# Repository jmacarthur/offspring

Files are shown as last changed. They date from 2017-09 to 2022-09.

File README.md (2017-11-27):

# Millihertz Model F ("Offspring")

This is a project to create a working replica of the Manchester small-scale experimental machine, otherwise known as the Manchester Baby.

It will be implemented fully mechanically, that is, without any electronic or electric components. All power must be taken from a single rotating shaft input.

The finished machine should be a complete, binary-compatible implementation of the original SSEM, capable of running the same programs.

It will be significantly slower than the original machine. It is meant to operate at about one cycle every 10 seconds (100mHz) compared to the 1kHz+ operation of the original machine.

The machine is not intended to be a useful tool; it's done mainly for fun, and to act as a visual demonstration of the operation of a stored-program computer.

## Overview diagram

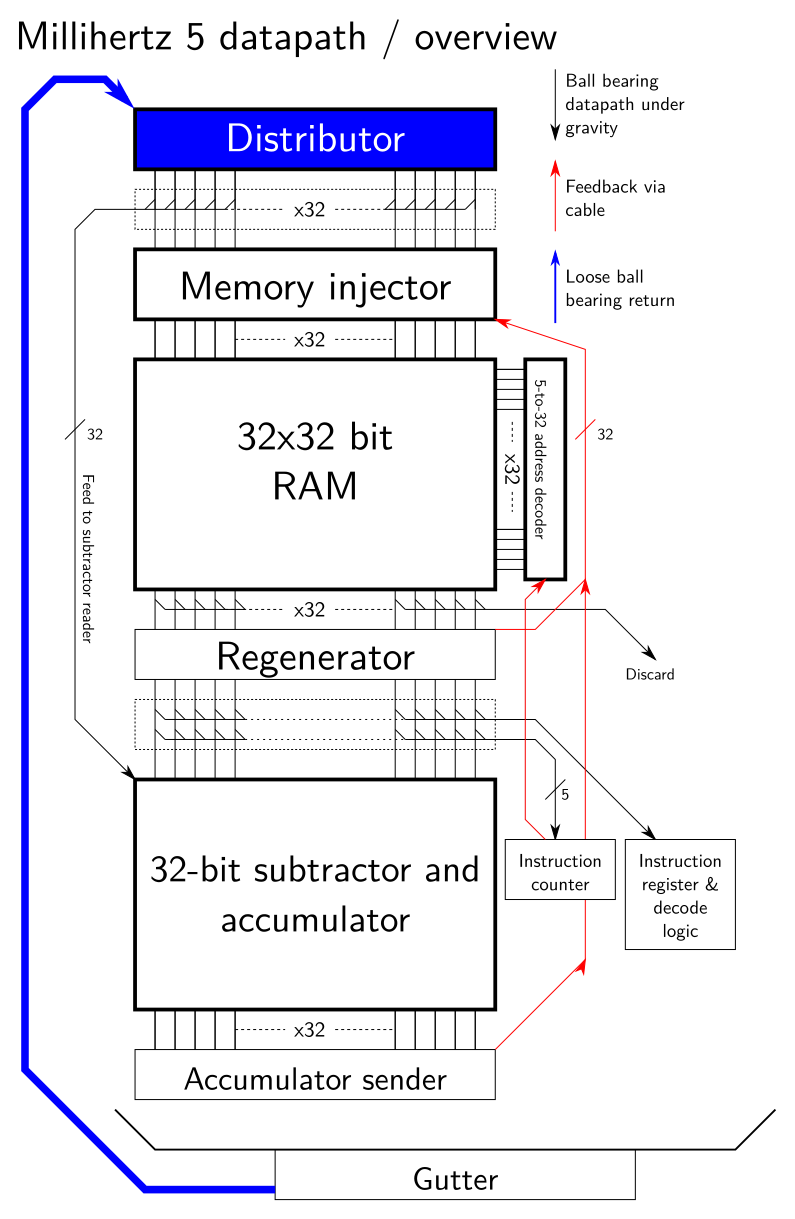
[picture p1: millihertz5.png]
Overview diagram


The machine is organised to take as much advantage of gravity as possible. The datapath runs down the machine, from the distributor at the top to the memory and then into the subtractor and accumulator. It is 32 bits wide, as was the original SSEM.

The major parts of the design have their own description pages in `docs/`.

* [Memory](docs/vertical-memory.md) - a 32x32 bit random-access memory, with address decoder.
* [Subtractor-accumulator](docs/subtractor-accumulator.md) - remembers its current value and subtracts whatever ball bearings are passed to it - a ball bearing in column 4 subtracts 16 from the accumulator, for example. Subtraction is the only arithmetic operation needed.

Parts not yet described are:

* The distributor, at the top of the machine, which measures out exactly 32 ball bearings and spreads them apart so they are the right pitch to enter the memory cell
* The memory injector, which allows selected ball bearings into the memory. There are 32 cables or rods connecting the regenerator (below) to the injector. When one is pulled down, the injector releases one of the ball bearings (which came out of the distributor) into the memory. There's also a separate control to discard any unused ball bearings in the injector.
* The regenerator samples the data coming out of the memory and pulls the rods leading to the injector, effectively sending the same pattern back into the top of the memory. This is important as reading is a destructive operation on the current memory.
* A series of diverters can send the data to the subtractor-accumulator, or the program counter, or the instruction register.
* A second regenerator below the subtractor-accumulator reads the values in the accumulator and sends them to the injector, for use in store operations.

Finally, at the bottom, all discarded ball bearings are collected and recirculated (perhaps by conveyor belt) to the distributor.

# Directories

* `scad` - CAD files in OpenSCAD format
* `diagrams` - high-level 2D drawings in DXF format for reference - showing interfaces between parts as well as some concept sketches.
* `docs` - Descriptions of parts with illustrative (not authoritative) diagrams, and reports on past experiments and prototypes.
* `lasercut-tests` - Laser cutting files generated from OpenSCAD are committed here to go alongside reports on prototypes in the `docs` directory. These should not be used other than as a reference for those documents.

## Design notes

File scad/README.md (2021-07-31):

# Index of OpenSCAD files

## Components, roughly in order from top to bottom

* octo-distributor-5.scad - current combined injector which can selectively pass ball bearings into memory and divert them to the subtractor.
* vertical-memory-2.scad - current candidate for vertical, 8x8 memory.
* decoder.scad - 16 word memory address decoder, placed alongside the memory.
* planar-diverter.scad - for diverting memory output to accumulator, PC and instruction decoder, and also the first regenerator
* subtractor.scad - subtractor/accumulator unit, used for both the main accumulator and PC
* memory-sender-3.scad - transmits memory addresses back up to the decoder.
* sequencer.scad - Main timing cam and instruction decoder.

## Assemblies

TBC

## Library files

* regenerator.scad - Common parts for the two regenerators.
* globs.scad - Constants for all files, such as the diameter of ball bearings.
* generic_conrods.scad - for producing rounded rectangles (stadia) with holes in each end, used as connecting rods.
* interconnect.scad - for connecting Bowden cables to other moving parts.

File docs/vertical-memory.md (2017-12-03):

# Vertical memory unit

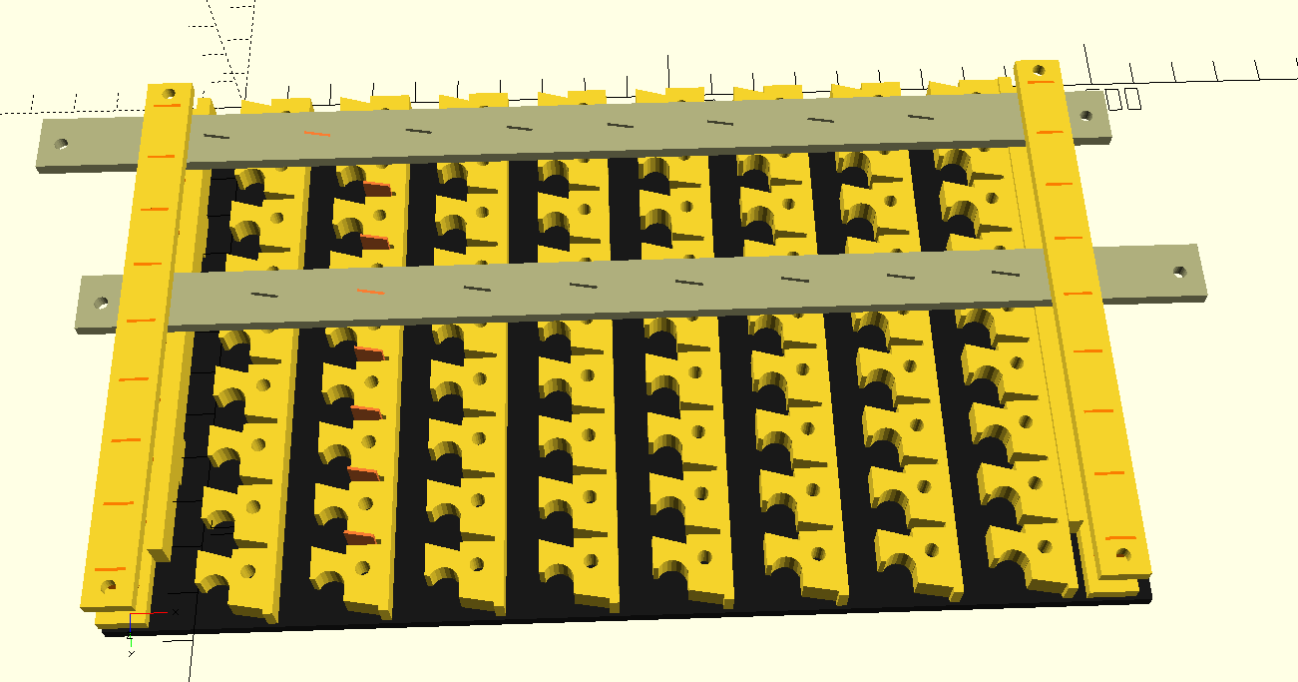
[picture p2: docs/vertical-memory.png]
Vertical memory rendering


The above rendering shows an example 8x8 memory cell. Two grey 'row select' bars are shown - there would normally be eight, but most have been removed to show the working. Most of these row select bars are pushed to the right. One, the selected row, is pushed to the left. Eight short strips of brass are embedded into the selector bars, which normally sit in a small pocket in the RAM. When pushed right, the brass strips enter the long channels in the memory, where they will intercept ball bearings rolling down that channel.

The following GIF (made with box2djs) shows the priciple of operation, for a 4x4 cell:

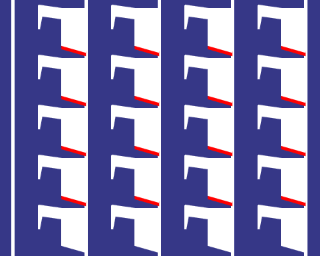
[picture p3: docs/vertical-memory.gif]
Vertical memory animation


To write data into the memory, one row is selected by pushing the corresponding row left, and a pattern of ball bearings is dropped into the channels running down the memory. A ball bearing represents a binary '1' and no ball bearing represents zero. When the ball bearings reach the selected row, the ball bearing is deflected right and into a small storage area.

When the selected row is returned to its normal position, the brass strip passes underneath the captured ball bearing, lifting it slightly but leaving it in its position.

The ball bearings remain in that row until the same row is selected again. When a row is selected while there is data in it, that data is pushed to the left and falls down the channel and out of the bottom of the RAM module. In that manner, the data stored when the row was initially selected is now read out of the memory. Reading is destructive; if you want to keep the same value in memory, you must duplicate the pattern of ball bearings and feed into the top of the RAM unit again. Magnetic core memory also had destructive reads, and regenerated memory locations in a similar way.

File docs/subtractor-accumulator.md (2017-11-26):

# Subtractor-accumulator unit

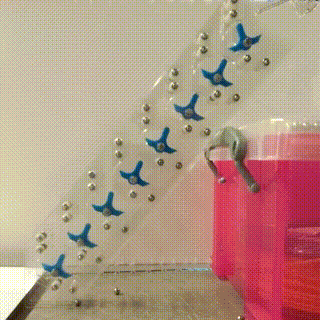
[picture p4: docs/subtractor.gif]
Subtractor video


The subtractor-accumulator sits below the memory, after the memory discard and splitters which divert to the intruction counter and register. The inverted T-shaped pieces rotate left or right to represent 1 or 0 respectively. Dropping a ball bearing into any of the input columns subtracts that value from the accumulator (the right hand column is 1, and the left 128). Subtracting 1 from 0 results in the ball bearing falling left and into the next column, so it leaves 1 in its original column and subtracts twice its value from the next column to the left. This continues until the ball bearing subtracts 1 from 1, at which point it falls to the right, or overflows out of the left of the machine.

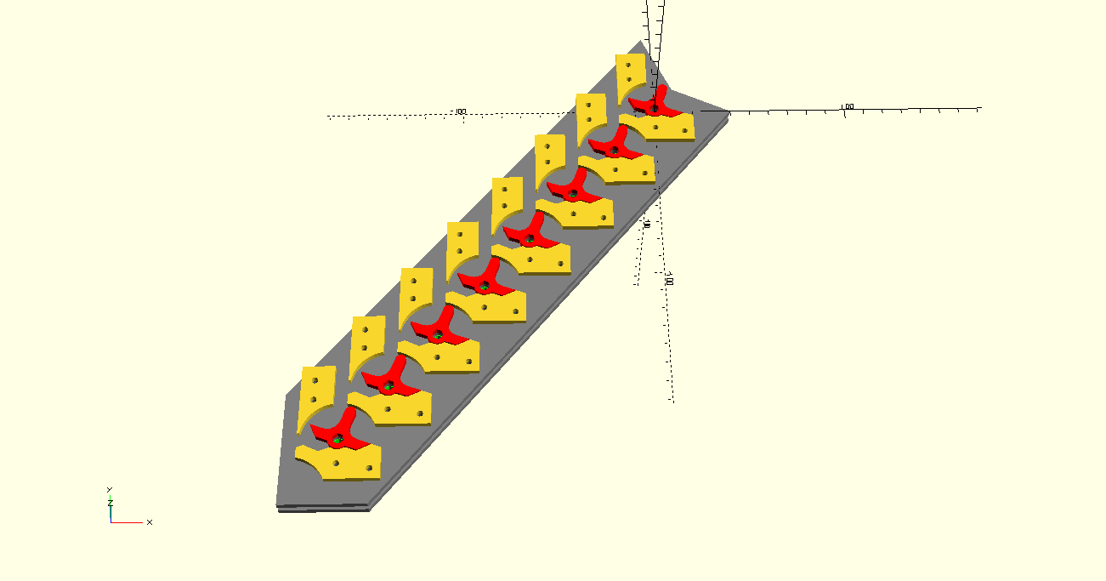
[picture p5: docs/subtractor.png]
Subtractor rendering


The design of the subtractor means it maintains its value automatically, so it's not necessary to keep a separate acumulator.

This is not my own design; there are several examples of cascading binary adders like this on the internet (TODO: where?). I've made a couple of modifications: The input senses are reversed so it functions as a subtractor rather than an adder, and it also has a second plane which can be used to copy the value in it without altering it. This requires 32 ball bearings to be dropped in on the 'read' plane, and these also come from the distributor, via the diverter valve just below it.

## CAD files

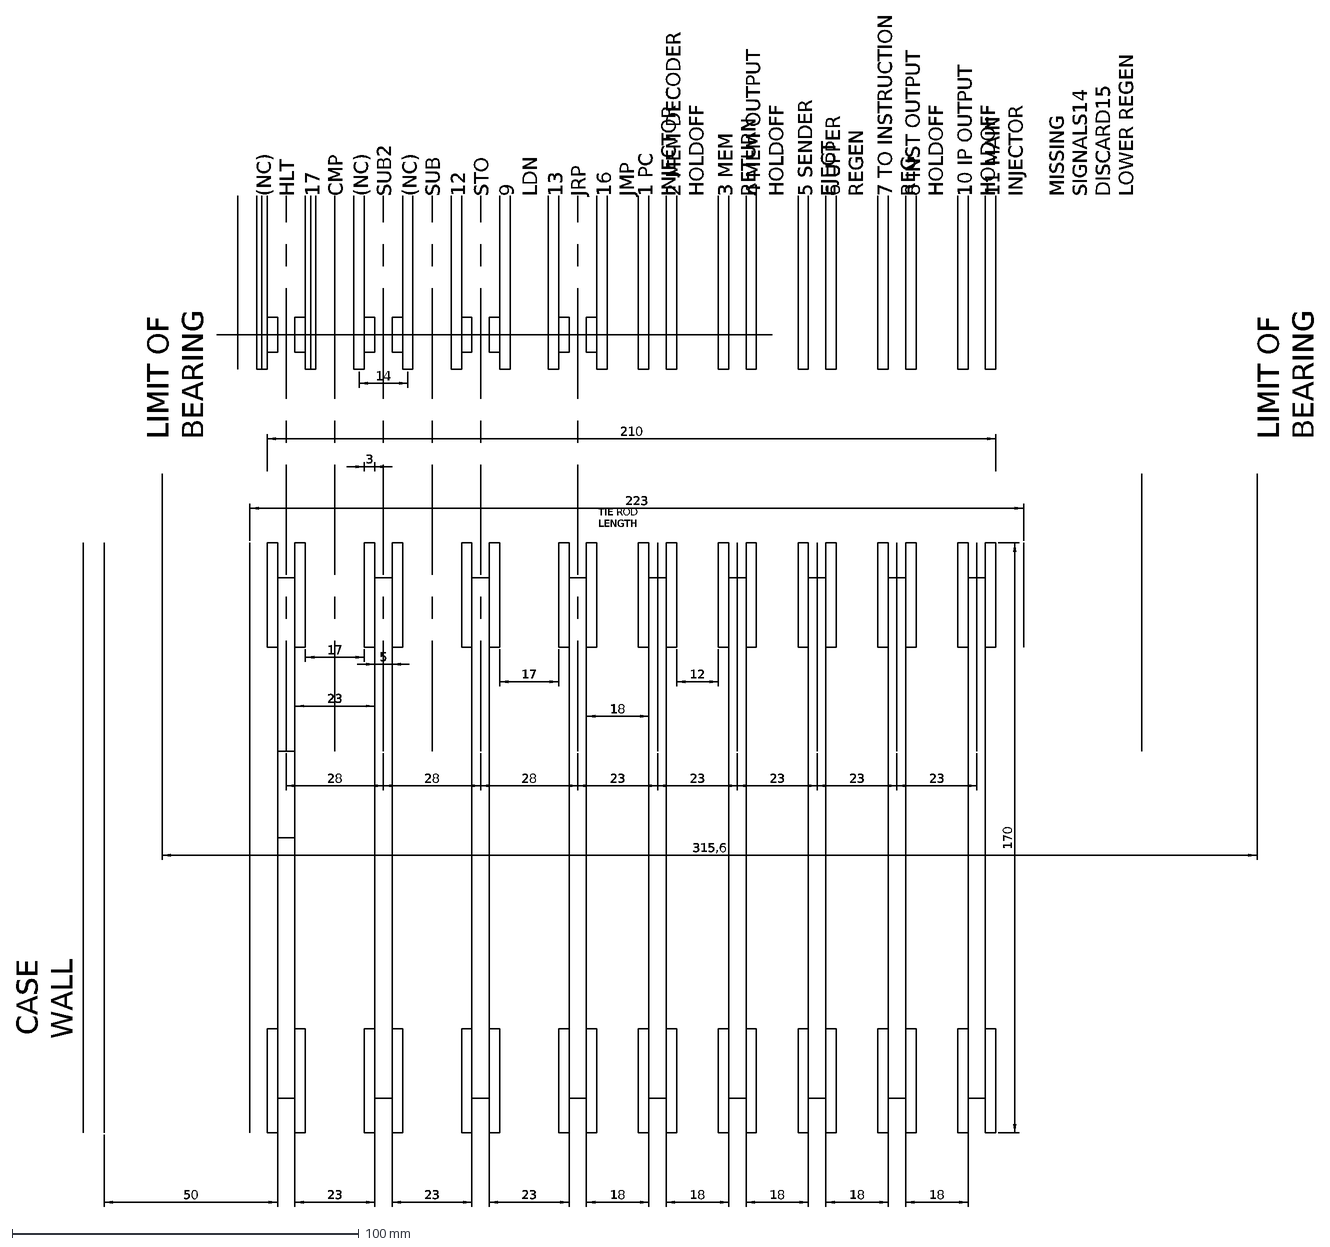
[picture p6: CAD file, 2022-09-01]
diagrams/camshaft2.dxf
28
3
14
23
210
LIMIT OF BEARING
315,6
18
5
17
12
170
16 JMP
13 JRP
9 LDN
12 STO
(NC) SUB
(NC) SUB2
17 CMP
(NC) HLT
223
TIE ROD LENGTH
1 PC INJECTOR
2 MEM DECODER HOLDOFF
3 MEM RETURN
4 MEM OUTPUT HOLDOFF
5 SENDER EJECT
6 UPPER REGEN
7 TO INSTRUCTION REG
8 INST OUTPUT HOLDOFF
10 IP OUTPUT HOLDOFF
11 MAIN INJECTOR
MISSING SIGNALS 14 DISCARD 15 LOWER REGEN
CASE WALL
50

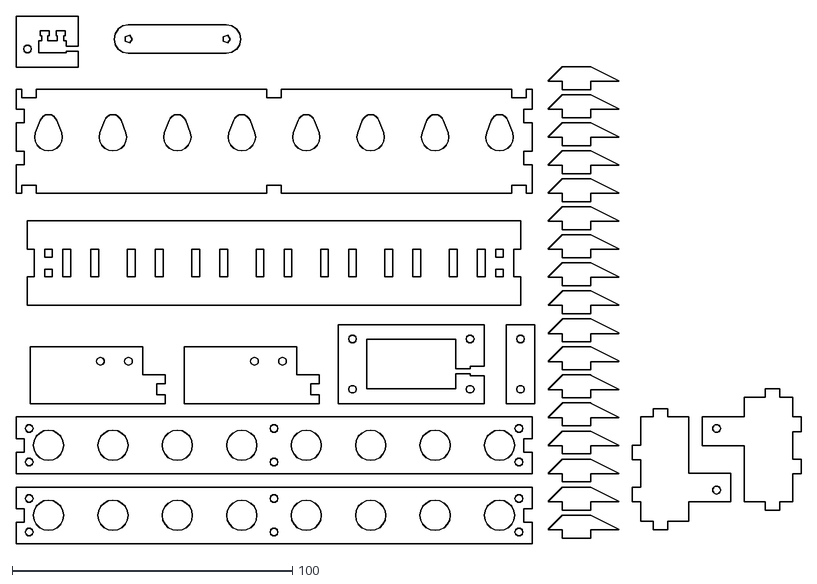
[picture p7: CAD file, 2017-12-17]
lasercut_tests/diverter-laser.dxf
280.2 x 188.2

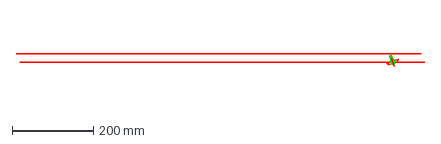
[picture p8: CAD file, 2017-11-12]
toggles.dxf
1008.0 x 30.4 mm

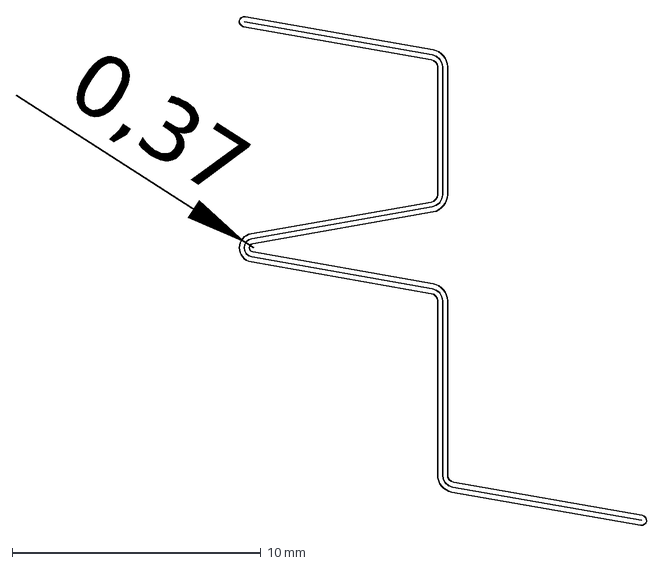
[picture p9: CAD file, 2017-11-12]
f-shape.dxf
0,37

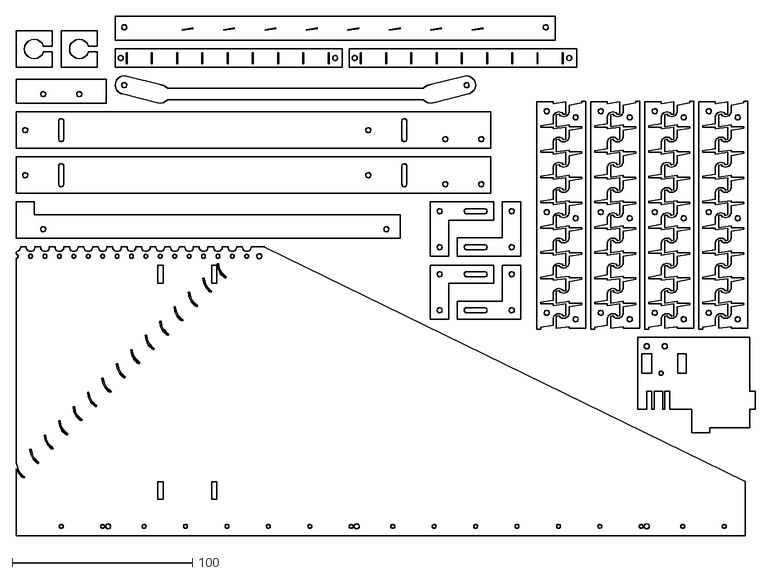
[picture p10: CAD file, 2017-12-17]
lasercut_tests/distributor-laser-2.dxf
410.2 x 288.2

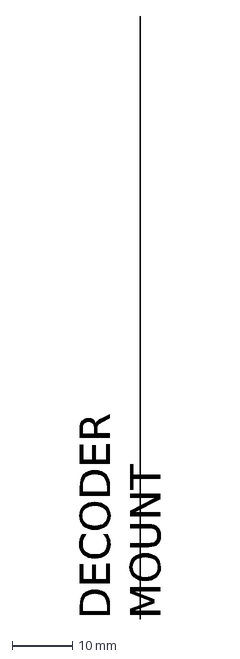
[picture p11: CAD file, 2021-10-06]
diagrams/memory-sender-mounting.dxf
DECODER MOUNT

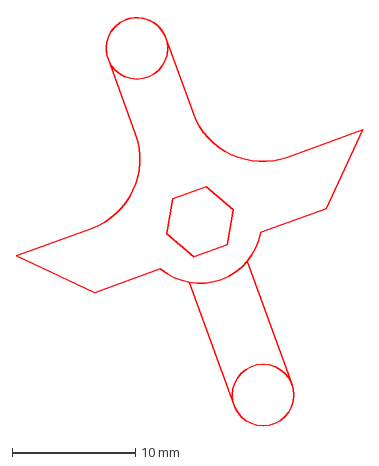
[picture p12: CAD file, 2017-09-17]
input-toggle.dxf
28.2 x 33.3 mm

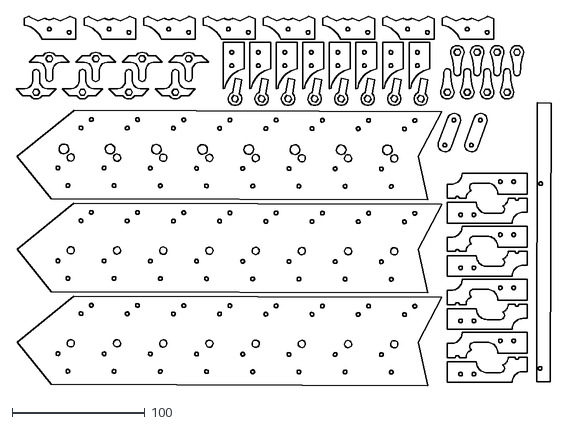
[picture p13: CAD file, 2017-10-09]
lasercut_tests/test-subtractor-v1.dxf
403.2 x 278.2

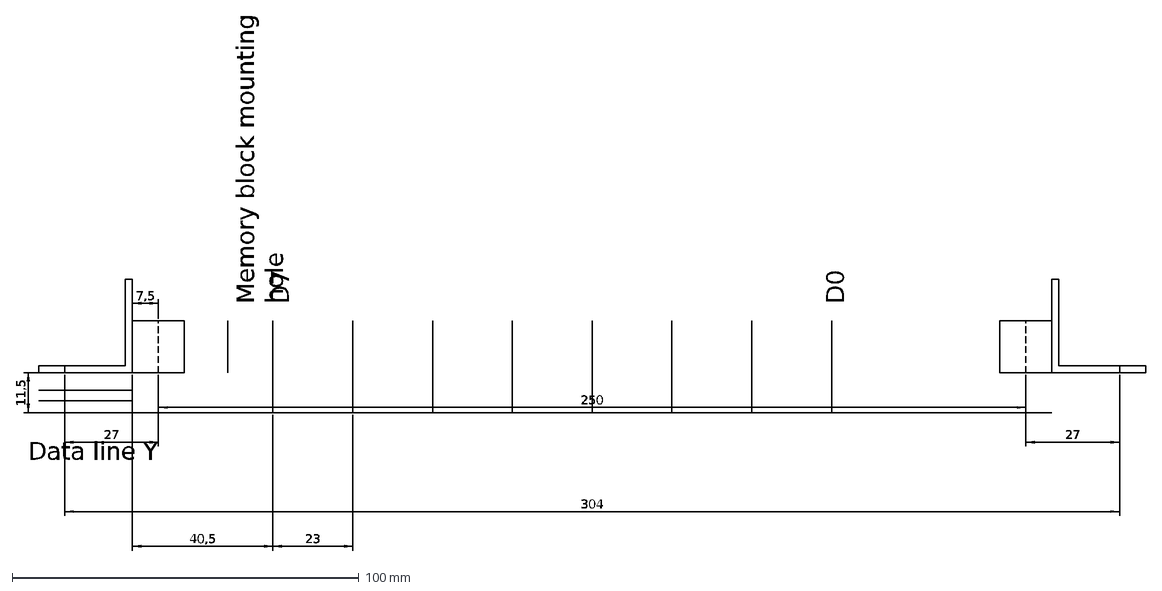
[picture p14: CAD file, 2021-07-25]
diagrams/rail_mouting.dxf
250
27
304
7,5
Memory block mounting hole
Data line Y
D7
D0
40,5
11,5
23

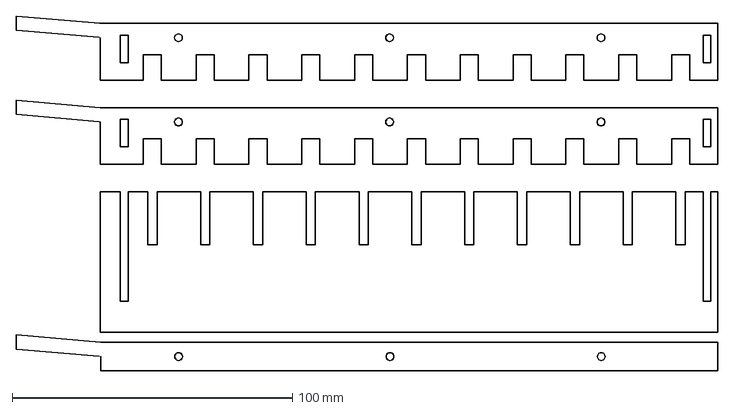
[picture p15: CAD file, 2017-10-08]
lasercut_tests/test-injector-v2.dxf
250.3 x 126.6 mm

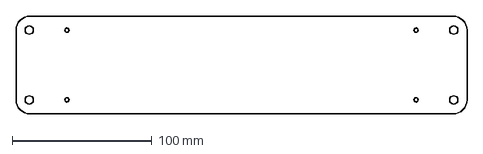
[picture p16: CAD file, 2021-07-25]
diagrams/rail_separator_plate.dxf
323.0 x 70.0 mm

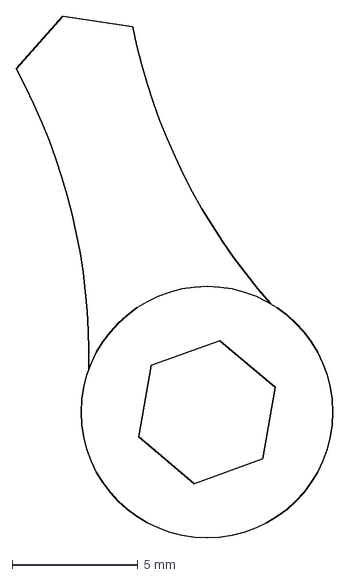
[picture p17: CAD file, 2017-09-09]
output-toggle.dxf
12.6 x 20.7 mm

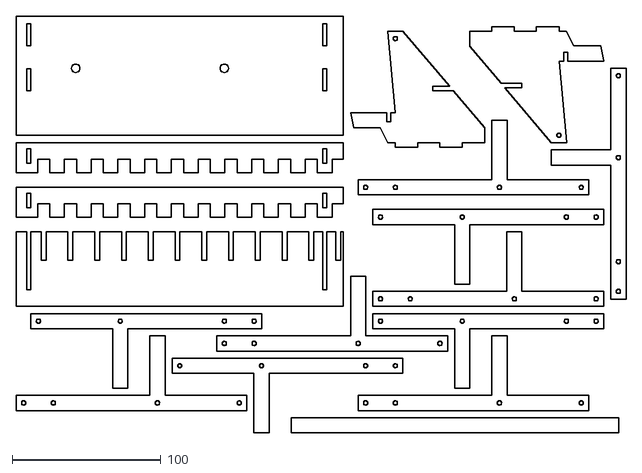
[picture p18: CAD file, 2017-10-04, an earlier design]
lasercut_tests/test-injector-v1.dxf
410.2 x 280.2

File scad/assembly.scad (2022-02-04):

use <vertical-memory-2.scad>;
use <octo-distributor-6.scad>;
use <regen-diverter.scad>;
use <decoder.scad>;
include <globs.scad>;
use <infra.scad>;
use <stacked-subtractor.scad>;
use <base-regen.scad>;

use <sequencer.scad>;
use <memory-sender-4.scad>;
module memory_mounting_plate() {
  x1 = 100; // coord of first openbeam rail centre
  x2 = x1+20; // coord of first memory mounting hole
  y1 = 280;
  difference() {
    cube([420,5,300]);
    // Openbeam mounting holes
    translate([x1,-1,y1]) rotate([-90,0,0]) cylinder(d=3,h=10);
    translate([x1+250,-1,y1]) rotate([-90,0,0]) cylinder(d=3,h=10);

    // Memory mounting holes
    translate([x2,-1,y1]) rotate([-90,0,0]) cylinder(d=3,h=10);
    translate([x2+200,-1,y1]) rotate([-90,0,0]) cylinder(d=3,h=10);
    // Decoder mounting holes
    for(y=[0:2])
    translate([x1+250+47, -1, y1-17.5-119*y]) rotate([-90,0,0]) cylinder(d=10,h=10);
  }
}


module openbeam() {
  color([0.3,0.3,0.3]) cube([15,15,1000]);
}
memory_mount_z = 800;

translate([0,0,1100]) injector_assembly();
translate([22.5,-5,memory_mount_z+158]) rotate([90,0,0]) memory_assembly();
translate([22.5,-5,memory_mount_z+10]) rotate([90,0,0]) memory_assembly();
translate([329.5,35,memory_mount_z+158+124.5]) rotate([0,90,0]) address_decoder();

translate([angle_iron_internal_spacing,0,0]) perforated_angle();
translate([0,0,0]) rotate([0,0,90]) perforated_angle();

openbeam();
translate([angle_iron_internal_spacing-15, 0 ,0]) openbeam();

color([0,0,0.9,0.5]) translate([-100+7.5,-5,memory_mount_z]) memory_mounting_plate();

// Indicate where memory input is
//color([0,1,1]) translate([data7_x, -11.5, 780]) cylinder(d=ball_bearing_diameter, h=50);


translate([0,0,550]) stacked_subtractor();

translate([0,-28,300]) rotate([0,0,-90]) base_regen(0);

translate([0,-130,100]) {
  sequencer_assembly();
  casing();
}

translate([350,30,350]) sender();

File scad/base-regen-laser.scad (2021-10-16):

use <base-regen.scad>;


backing_plate_2d();
kerf = 0.08;
$fn=50;


offset(r=kerf) {
  translate([0,50]) 
    for(i=[0:15]) {
      translate([i*20,0]) rotate(90) input_coupler_2d();
    }
  
  translate([0,110]) 
    for(i=[0:7]) {
      translate([i*70,0]) input_arc_2d();
      translate([i*50,100]) output_arc_2d();
    }
}

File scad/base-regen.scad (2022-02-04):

include <globs.scad>;

radius = 40;
input_arc_thickness = 5;

input_x = 48; // Position of input relative to left edge of openbeam; 48 matches subtractor

centre_x = input_x-10; // Centre line for arms

module sector_2d(min_radius, max_radius, degrees)
{
  // degrees must be <= 90
  intersection() {
    difference() {
      circle(r=max_radius);
      circle(r=min_radius);
      rotate(degrees) square([max_radius+1, max_radius+1]);
    }
    square([max_radius+1, max_radius+1]);
  }
  
}


module input_arc_2d() {
  difference() {
    union() {
      sector_2d(radius-5, radius+3, 90);
      sector_2d(radius-10, radius+3, 70);
      translate([10,-5]) square([radius-10+3+20, 10]);
      translate([10,-5]) square([radius-10+3+25, 5]);
      rotate(36.5) translate([30,-5]) square([17, 10]);
    }

    // Angle the end to hold the bearing in place durig push
    polygon([[0,radius-5], [3, radius+3], [0, radius+3]]);
    translate([15,0]) circle(d=3);
    translate([35,0]) circle(d=3);
  }
}

module input_arc()
{
  rotate([-90,0,0]) linear_extrude(height=input_arc_thickness) input_arc_2d();
}

module output_arc_2d() {
  arc = 80;
  difference() {
    union() {
      sector_2d(radius-3, radius+3, arc);
      rotate(10) sector_2d(radius-6, radius+3, arc-10);
      rotate(arc) translate([0,-5]) square([radius+3+40, 10]);
      circle(d=10);
    }

    for(x=[0:5]) {
      rotate(arc) translate([radius+3+x*5+10,-6]) square([1,3]);
      rotate(arc) translate([radius+3+x*5+10,3]) square([1,3]);
    }

    circle(d=3);
  }
}

module output_arc()
{
  rotate([0,100,0]) rotate([-90,0,0]) linear_extrude(height=3) output_arc_2d();
}

module input_coupler_2d() {
  difference() {
    union() {
      translate([0,-5]) square([45,10]);
      circle(d=10);
    }
    translate([15,0]) circle(d=3);
    translate([35,0]) circle(d=3);
    circle(d=3);
  }
}

module backing_plate_2d(shift) {
  difference() {
    translate([0, 0]) square([250+15,41]);
    for(x=[0,250]) {
      translate([7.5+x,10]) circle(d=3);
      translate([7.5+x,30]) circle(d=3);
    }
    translate([shift,0]) {
      for(i=[0:7]) {
	translate([centre_x-2+pitch*i, 11]) offset(r=1) square([4,18]);
      }
      for(i=[1,6]) {
	translate([centre_x+pitch*i+pitch/2, 10]) circle(d=3);
      }
    }
  }
}

module backing_plate(shift) {
  rotate([90,0,0]) rotate([0,90,0]) linear_extrude(height=3) backing_plate_2d(shift);
}

module housing() {
  height = 17;
  depth = 50;
  difference() {
    union() {
      translate([-depth/2,0,-radius-6]) cube([depth,pitch*8+9,height]);

      // Axle posts
      hull() {
	translate([-10,0,-radius-5]) cube([20,pitch*8+5,10]);
	rotate([-90,0,0]) cylinder(d=10,h=pitch*8+5);
      }
      // Catchment area
      for(i=[0:7]) {
	difference() {
	  translate([-depth/2,pitch/2+pitch*i,-40]) cube([20,20,20]);
          // Drain cone, +Y
          translate([0,pitch/2+pitch*i,0]) rotate([-90,0,0]) cylinder(h=18, r1=radius-7, r2=radius-11, $fn=200);
	}
      }
    }
    for(i=[0:7]) {
      // Main channel
      translate([0,pitch/2+pitch*i-3.5,0]) rotate([-90,0,0]) cylinder(h=7, r=radius+4, $fn=200);

      // Drain cone, +Y
      translate([0,pitch/2+pitch*i,0]) rotate([-90,0,0]) cylinder(h=12, r1=radius-3, r2=radius-10, $fn=200);
      // Spacing cylinder, -Y
      translate([0,pitch/2+pitch*i-7,0]) rotate([-90,0,0]) cylinder(h=5, r=22, $fn=200);
    }

    
    // Drain holes
    for(i=[0:7]) {
      translate([0,pitch/2+pitch*i-3.5,-radius-10-1]) cube([7,7,20]);
    }

    // Assistance slope for the drain holes
    for(i=[0:7]) {
      translate([-7,pitch/2+pitch*i-3.5,-radius-4+0.4]) rotate([0,10,0]) cube([8,7,7]);
    }
    // Axle hole
    translate([0,-5,0]) rotate([-90,0,0]) cylinder(d=3.2, h=pitch*8+50);

    // Mounting holes
    for(i=[2,7]) {
        #translate([-26, pitch*i, -radius-6+10]) rotate([0,90,0]) cylinder(d=3, h=20);
    }

  }
}

module regen_input_coupler_2d() {
  difference() {
    translate([centre_x-pitch/2,0]) square([pitch*8,20]);
    for(i=[0:7]) {
      translate([centre_x+pitch*i-2.5,7.5]) square([5,5]);
    }
    for(i=[1,4,7]) {
      translate([centre_x+pitch*i-pitch/2,5]) circle(d=3);
      translate([centre_x+pitch*i-pitch/2,15]) circle(d=3);
    }
  }
}

module regen_input_coupler() {
  rotate([0,90,0]) rotate([0,0,90]) linear_extrude(height=5) regen_input_coupler_2d();
}

module base_regen(shift)
{
  translate([0,shift,0]) {
    translate([0,centre_x-pitch/2,0]) housing();
    for(i=[0:7]) {
      color([0.5,0,0]) translate([0,centre_x+pitch*i-1.5,0]) output_arc();
      color([0,1,0]) translate([0,centre_x+pitch*i-input_arc_thickness/2,0]) input_arc();
      
      color([0.4,0.4,0.4]) translate([0, centre_x+pitch*i-input_arc_thickness/2,0]) rotate([90,0,0]) linear_extrude(height=3) input_coupler_2d();
       color([0.4,0.4,0.4])  translate([0, centre_x+pitch*i+input_arc_thickness/2+3,0]) rotate([90,0,0]) linear_extrude(height=3) input_coupler_2d();
    }
    translate([-3.5,centre_x,-35]) sphere(r=ball_bearing_radius, $fn=40);
  }
  color([0,1,0]) translate([-25-3,0,-radius-6]) backing_plate(shift);

  translate([63,0,-7.5]) regen_input_coupler();

}

// Illustrate data
color([1,0,0]) translate([0,input_x,0]) cylinder(r=1, h=100);

base_regen(0);

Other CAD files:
diagrams/memory_block_drilling_diagram.dxf
Overview3.dxf
diagrams/top_mounting_board.dxf
scad/decoder-laser-moving.scad
scad/base-regen-test.scad
scad/decoder-laser-static.scad
scad/decoder.scad
scad/diverter-accessories.scad
scad/diverter-end-clip.scad
scad/diverter-parts.scad
scad/dropper.scad
scad/frame_coupler.scad
scad/generic_conrods.scad
scad/globs.scad
scad/handle.scad
scad/infra.scad
scad/interconnect.scad
scad/memory-decoder-standoff.scad
scad/memory-sender-3-laser.scad
scad/memory-sender-3.scad
scad/memory-sender-4.scad
scad/misc.scad
scad/octo-distributor-5-laser.scad
scad/octo-distributor-5.scad
scad/octo-distributor-6.scad
scad/planar-diverter-laser.scad
scad/planar-diverter-sheet1.scad
scad/planar-diverter-sheet2.scad
scad/planar-diverter.scad
scad/regen-diverter.scad
scad/regenerator.scad
scad/sequencer-cam-laser.scad
scad/sequencer-laser.scad
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

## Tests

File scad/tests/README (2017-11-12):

This directory is for SCAD files which are meant for test prints or
laser cuts.  They are usually cut-down versions of larger files in the
parent directory and should not be used for reference.

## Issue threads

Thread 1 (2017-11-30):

Distributor/memory and subtractor are different pitches

jmacarthur, 2017-11-30:
Subtractor is based on a 22mm pitch and the memory cell and distributor are 23mm pitch (based on the memory cell, 7+7+7 memory cell and 2mm joining bar). Adjust the subtractor so it works at 23mm pitch.

jmacarthur, 2017-11-30:
Fixed subtractor in e4ba957.

Closed 2017-11-30.

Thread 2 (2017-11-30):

Distributor doesn't include inter-cell split

jmacarthur, 2017-11-30:
We're expecting to have a split lane between the each 16-bit half of the memory. Decide how big that gap is and alter the distributor to suit.

jmacarthur, 2017-12-04:
Added a gap of 50mm (25mm per side) at a2a4829.

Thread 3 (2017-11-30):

Toggles on subtractor are too low

jmacarthur, 2017-11-30:
The input toggles on the subtractor are set slightly too low; the top of the sideways arms should be raised by 0.5-1mm to avoid the chance of the ball bearing sticking on leaving.

jmacarthur, 2017-11-30:
Raised by 0.25mm in e4ba9572e6d586c0c28d41b8639ad076c931e03e.
Needs re-cut and test to determine if that's enough.

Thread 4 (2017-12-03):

Holding area on memory is too low

jmacarthur, 2017-12-03:
The ball bearing sits slightly too low in the holding cell, which means the selector rod can jam occasionally when it's returned. We should raise the right-hand side slightly.

jmacarthur, 2019-01-09:
This refers to an older version of the memory and no longer applies.

Closed 2019-01-09.

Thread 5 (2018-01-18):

Decoder needs central support for the follower lever axle.

jmacarthur, 2018-01-18:

jmacarthur, 2018-01-20:
Fixed in bdb592d331bac953b56dcd6f1904ddd44ae21d9c

Closed 2018-01-20.

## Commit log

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2017-09-06 Reposition entire drawing to be inside printable range
    [Overview3.dxf]
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2017-09-09 Redo accumulator to make it shorter
    [Overview3.dxf]
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2017-09-09 More fixes to memory
    [3d_assembly.scad]
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2017-09-17 Remove the flat bus connectors and extend the existing arms
    [memory-injector.scad]
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2017-09-17 Thicken a weak part of the support plate
    [memory-injector.scad]
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2017-10-04 Update lasercut to lay out test injector properly
    [lasercut.scad]
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2017-10-08 pipe_holder_bar is no longer used
    [memory-injector.scad]
2017-10-08 Turn input rail into a 2D module and add distance adjustment holes
    [memory-injector.scad]
2017-10-08 Add new input rail to injector 2D laser layout
    [memory-injector.scad, test-injector-lasercut.scad]
2017-10-08 Move test injector v1 laser cut file into its own directory
    [test-injector-v1.dxf]
2017-10-08 Add test injector V2.
    This is a modification to V1 to use 6.28mm diameter ball bearings and
    smaller spacing for pipe connectors. Only the modified parts from V1
    are included. There is also a manually added ball bearing input ramp.
    [test-injector-v2.dxf]
2017-10-09 Start the subtractor file with the input toggle
    [subtractor.scad]
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2017-10-09 Reset layer
    [subtractor.scad]
2017-10-09 Shrink support plates and make reset bar thicker
    [subtractor.scad]
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2017-10-09 Adjust hex bar to measured size and regenerate subtractor test V1
    [subtractor.scad, test-subtractor-v1.dxf]
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2017-10-19 Add former for memory cell using brass strip
    [memory-cell-mould.scad]
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2017-10-23 Add toggles.dxf, a component of the overview dxf
    [toggles.dxf]
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2017-10-23 Add f-shape.dxf, which is just the outline of a single memory cell, for import into SCAD
    [f-shape.dxf]
2017-10-23 Add test-memory-line.scad, used to test cutting for brass strip
    [test-memory-line.scad]
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2017-11-11 Add some test SCAD files into the scad/tests directory
    [column-selector-test.scad, memory-cell-4-test.scad]
2017-11-11 Add memory line folder scad (no longer relevant)
    [memory-line-folder.scad]
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2017-11-11 Add comments to some of the memory files, stating that the diagonal system is now obsolete.
    [memory-cell-16.scad, memory.scad]
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2017-11-11 Correct for extra row and add mounting holes for combs
    [vertical-memory.scad]
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2017-11-12 Injector: Adjust strip sizes, add side wall and kerf to laser layout
    [vertical-memory-laser.scad, vertical-memory.scad]
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2017-11-30 Adjust subtractor pitch to 23mm and fix issues arising
    [subtractor.scad]
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2017-12-04 Add centre-gap in distributor
    The example wires in the second stage are now mostly calculated by guessing values - a cleanup is needed
    [distributor.scad]
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2017-12-09 Memory and distributor improvements
    Distributor: Add holes at the top to allow the stage1 wires to fold
    under their plate.
    Memory: Increase input clearance and reduce the number of alignment holes.
    [distributor.scad, vertical-memory.scad]
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2017-12-10 Distributor: Explain echo output, add comments, fix whitespace
    [distributor.scad]
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2017-12-17 Corrections to diverter - connection of rotating support and separator plates
    [diverter.scad]
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2017-12-28 Minor fixes to the distributor riser
    [distributor.scad]
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2018-01-13 Shorten output and top plate
    [octo-distributor.scad]
2018-01-14 Update comments in globs - we have two sizes of ball bearing!
    [globs.scad]
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2018-01-14 Add decoder, a very simplified version of the selector array logic from an earlier project
    [decoder.scad]
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2018-01-14 Correct comment on xBars
    [decoder.scad]
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2018-01-14 Move everything up so it no longer fouls the frame
    [decoder.scad]
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2018-01-14 Add t-slot on the end of enumerators so we can chain them
    [decoder.scad]
2018-01-14 Correct some col/row confusion for the vertical memory
    [vertical-memory.scad]
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2018-01-14 Add a reinforcing strip
    [decoder.scad]
2018-01-14 Corrections to mounting holes/reinforcing strip
    [decoder.scad]
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2018-01-14 Fixes to lifter bar - measurements still done by eye, need proper fixing
    [decoder.scad]
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2018-01-18 Re-add whole decoder assmembly to 3D view and increase reinforcing slot size
    [decoder.scad]
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2018-01-20 Add some lever supports to the static part of the decoder laser file
    [decoder-laser-moving.scad]
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2018-01-20 Add follower axle reinforcement
    [decoder-laser-moving.scad, decoder-laser-static.scad, decoder.scad]
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2018-01-27 Add wood planks above and below injector and cut outs for end plates
    [injector.scad]
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2018-01-28 Diverter2: Reinforce control levers
    [diverter-v2.scad]
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2018-01-28 OctoInjector2: Misc fixes
    [octo-distributor-2.scad]
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2018-02-11 Hole for bias weights on injector; rearrange laser layout to fit on A3
    [injector-laser.scad, injector.scad]
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2018-04-17 Add ejector comb; rename plates for memory; clean up april-laser a bit
    [april-laser.scad, octo-distributor-4.scad, vertical-memory-2.scad]
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2018-04-17 Shorten regen, Add more pusher supports
    [base-regenerator.scad, regenerator.scad]
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2018-04-17 Corrections to april-laser layout, add extra regen output
    [april-laser.scad]
2018-04-18 Remove octo-distributor 1 and 2, no longer relevant
    [octo-distributor-2.scad, octo-distributor.scad]
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2018-04-25 Remove selector-test and add a README containing an index of all current OpenSCAD files
    [selector-test.scad]
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2018-05-07 octo5: Correct location of holes for comb support
    [octo-distributor-5.scad]
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2018-05-12 sender: Corrections to intake slope
    [memory-sender.scad]
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2018-05-12 Memory: flip returner so it's on the top plate
    [vertical-memory-2.scad]
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2018-05-19 Fix kerf
    [may-laser-2.scad]
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2018-05-26 Regen2: Add clearance
    [regen-2.scad]
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2018-05-28 Add may-laser-4.scad, a temporary commit to cut remaining pieces for the memory and injector
    [may-laser-4.scad]
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2018-05-28 Octo5: Remove 'output slopes' (no longer used)
    [octo-distributor-5.scad]
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2018-05-31 sender2: Shorten everything in the X dimension
    [memory-sender-2.scad]
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2018-06-06 Remove the regenerator from the regen-splitter altogether; it can be added with an openbeam bar
    [regen-splitter.scad]
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2018-06-06 octo-5: Use the new generic diverted output assemblies instead of the local ones
    [diverter-parts.scad, octo-distributor-5.scad]
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2018-10-06 Sequencer: Initial work on resetter box
    [sequencer.scad]
2018-10-06 Sequencer: Side plate for resetter.
    [sequencer.scad]
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2018-10-07 sequencer: Replace 50T gear with 75T gear
    [sequencer.scad]
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2018-12-28 Whitespace fixes
    [planar-diverter.scad]
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2018-12-28 Planar diverter: Add bowden cable clearance
    [planar-diverter.scad]
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2019-01-06 Planar diverter: Fix variable name
    [planar-diverter.scad]
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2019-01-06 Memory: Fix centre line hole through comb
    [vertical-memory-2.scad]
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2019-01-06 Memory: Adjust stator so it clips into the top plate instead of the combs
    [vertical-memory-2.scad, vertical-memory-laser.scad]
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2019-01-13 Planar diverter: No need for pipe exit plate to cover discard line
    [planar-diverter.scad]
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2019-01-13 Memory sender: Allow gap for reset bar
    [memory-sender-2.scad]
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2019-01-28 Add tabs to the bottom of the decoder for mounting to the sequencer
    [decoder.scad, sequencer.scad]
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2019-01-28 Adjust height of follower rods and drop rods, add hole for follower bearing
    [sequencer.scad]
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2019-02-17 Add small clearance to cam support discs
    [sequencer-laser.scad, sequencer.scad]
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2019-10-22 Correction to sequencer top case
    [sequencer.scad]
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2020-01-04 Replace subtractor's rear top output guard
    [subtractor.scad]
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2020-02-08 Correct follower spacing
    [sequencer.scad]
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2020-02-29 Correction to dropper code
    [dropper.scad]
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2021-07-25 Decoder: Fix lifter_bar_axles argument
    [decoder.scad]
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2021-07-25 Fix rail_mounting.dxf so the angle iron hole offsets are correct
    [rail_mouting.dxf]
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2021-08-04 ODS6: complete rewrite; replace lever with caged injector
    [octo-distributor-6.scad]
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2021-08-05 Regen-diverter.scad: Realign parts so ball bearing axis is at X=0; add output lever
    [regen-diverter.scad, subtractor.scad]
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2021-08-14 Regen-diverter: Significant rewrite; replace flap/hopper
    [regen-diverter.scad]
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2021-08-28 Regen-diverter: reduce clearance on pull bar
    [regen-diverter.scad]
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2021-08-28 regen-diverter: Add adjustment to the pull bar axle (since it didn't fit)
    [regen-diverter.scad]
2021-08-28 regen-diverter: Remove the diverter support plate since it's no longer used
    [regen-diverter.scad]
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2021-10-05 subtractor: remove pipe connectory, no longer required
    [subtractor.scad]
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2021-10-23 Regen: Adjust so we can take a shift parameter for the X axis
    [base-regen.scad, regen-diverter.scad]
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2021-10-23 Rename backing_plate to discard_backing_plate to avoid clash
    [regen-diverter.scad]
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2021-11-20 Subtractor: Add reverse reset lever
    [subtractor.scad]
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2021-12-04 sequencer.scad: widen input module to allow some clearance and thicker walls
    [sequencer.scad]
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2021-12-18 SCAD: add a couple of laser test files for regen and subtractor
    [base-regen-test.scad, subtractor-test.scad]
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2022-01-07 Remove memory-sender-2-laser.scad, no longer needed
    [memory-sender-2-laser.scad]
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2022-01-15 Sequencer: Correct cam diameters
    [sequencer.scad]
2022-01-15 Sequencer: Begin reset mechanism
    [sequencer.scad]
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2022-01-22 Sequencer: Back plate, reset crank, shortened sides
    [sequencer.scad]
2022-01-23 Sequencer: Add more holes in the case to bolt the sides together
    [sequencer.scad]
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2022-02-20 Memory-sender-4: add clearance
    [memory-sender-4.scad, octo-distributor-6.scad]
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2022-04-25 Sequencer: Remove some tiny features which would be difficult to laser cut
    [sequencer.scad]
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2022-09-09 Sequencer-laser.scad: Replace entire file, just using follower_comb now
    [sequencer-laser.scad]
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2023-01-26 Sequencer: Offset universal cams a bit to avoid collisions
    [sequencer.scad]
2023-01-26 Sequencer: Round the tops of the channels in the follower combs, to hopefully increase strength
    [sequencer.scad]
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2023-02-15 Small-sequencer: Add decoder, showing how we can add a decoder without extra space
    [small-sequencer.scad]
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2023-02-16 small-sequencer: move the decoder rods to the left, since the data comes out there
    [small-sequencer.scad]
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2023-02-16 small-sequencer: Trim instruction levers so we can activate them with ball bearings
    [small-sequencer.scad]
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2023-02-18 small-sequencer: Instruction decoder reset mechanism
    [small-sequencer.scad]
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2023-02-23 small-sequencer: Oops, got the width wrong
    [small-sequencer.scad]
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2024-02-26 Misc fixes to pulley plate
    [small-sequencer.scad]
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
